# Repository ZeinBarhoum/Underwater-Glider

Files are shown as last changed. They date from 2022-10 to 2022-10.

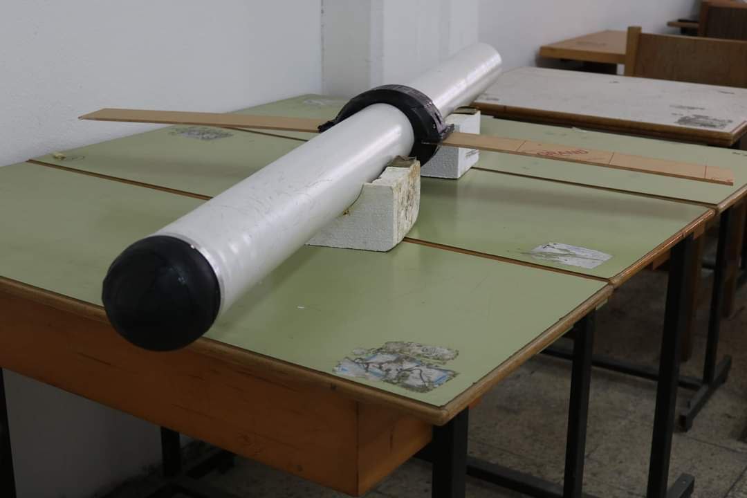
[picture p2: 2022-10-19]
Underwater glider.jpg

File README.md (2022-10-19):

# Underwater-Glider

This repository includes the design and source code files for the project "Underwater Glider"

Underwater gliders are underwater vehicles that don’t use any external propellers or thrusters.  

These vehicles are autonomous, and their motion depends on controlling the buoyancy-gravity force balance and the placement of the center of gravity.

Buoyancy is controlled using buoyancy engine (BE) which could operate in one of two ways:
  1-	Varying the mass of the vehicle by inhaling or exhaling the surrounding fluid (water).
  2-	Varying the volume of the vehicle by inflating or deflating an external balloon-shaped bladder
  
The BE used in this project is from the first type, and a tank is designed using syringes to accomplish this functionality.

To control the center of gravity, a moving mass (MM) system was designed which can change the center of gravity along the main axis by sliding the mass, and to change the center of gravity on the YZ plane, rotating the mass was the method of choice.

A full study and implementation were conducted in this project starting from designing, modeling and simulating and ending with manifacturing, testing and controling the underwater glider.

All the files are included in the repository and for further information please contact the authors of this project.

Zein Alabedeen Barhoum: zein.barhoum799@gmail.com
Rahaf Alshaowa: rahafalshaowa98@gmail.com

Note: this project was conducted to fulfill the requirements of Bachelor's degree in mechatronics engineering. And based on the implementation, report and presentation, a grade with honor of 96% was awarded to the authors of this project.

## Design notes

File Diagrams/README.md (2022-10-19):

# diagrams

In this folder, the pinout diagram of the circuit of the underwater glider is provided with specific diagrams for each electronic component used.
Three stepper were used with sizing of NEMA17, A4988 circuits were used (3 of them, one for each motor).
four hand-made leakage sensors were used in the two endings and the center of the glider. Moreover, limit switches were used to prevent the mechanical part from stepping out of their limits mechanically, two were used for each motor. 
As stated before, the beaglebone blue was used as the main controller, an therefore, its pinout diagram is provided.

Two power systems were used in the glider, one is 12V for the motors and the beaglebone. And 5V system for sensors and to provide power in the case of power outage in the 12V system.
The batteries used in addition to the charging circuits are shown in diagrams too.

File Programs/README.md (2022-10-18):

# Simulink Programs

the controller used in the underwater glider is the beaglebone blue which has an intertial measurment unit (IMU) which is the MPU-9250 that includes 
gyroscope,accelerometer and magnetometer. Moreover, an additional IMU which is the MPU-6050 was used. A fusion algorithm between these two IMUs were used to 
calculate the angular position (using Euler angles), in addition, the acceleration were also calculated to test depth calculation using acceleration data. 
The programs that were used to control the underwater glider were constructed using Simulink software with the beaglebone blue plugin.

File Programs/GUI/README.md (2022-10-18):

# GUI

An expermental GUI was created using MATLAB which interactc with the Simulink program to visualize the current position of the glider.

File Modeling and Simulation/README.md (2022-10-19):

# Modeling and Simulation

A modeling of the designed underwater glider was conducted, the mathmatical equations that formulate the motion of the vehicle depending on the 
input on the motor were analyzed and inputed into Matlab and Simulink to simulate the motion of the underwater glider under diffrent inputs.

The full model and simulation files are provided here.

Note: the Initialize.m file compute the symbolic inverse of multiple matrices in the model in order to avoid run-time calculations of matrix-inverse 
this dramatically decreases the time of the simulation.

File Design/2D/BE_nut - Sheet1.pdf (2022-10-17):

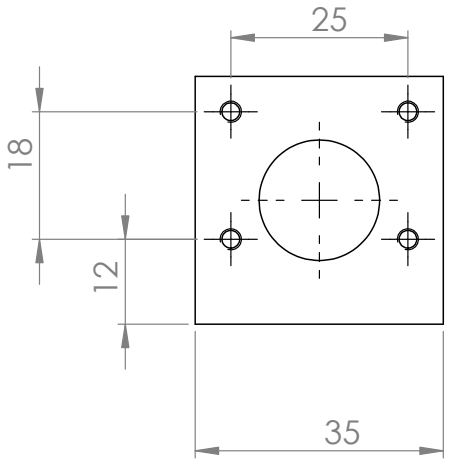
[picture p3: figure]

35

20

47

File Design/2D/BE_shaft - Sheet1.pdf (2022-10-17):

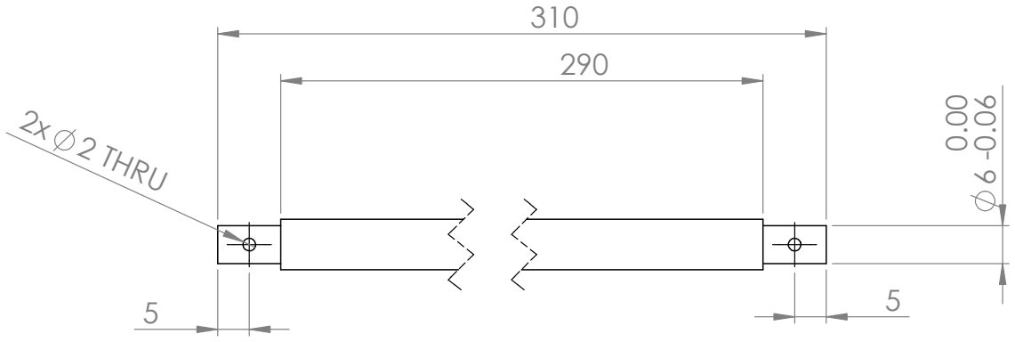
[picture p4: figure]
2 THRU

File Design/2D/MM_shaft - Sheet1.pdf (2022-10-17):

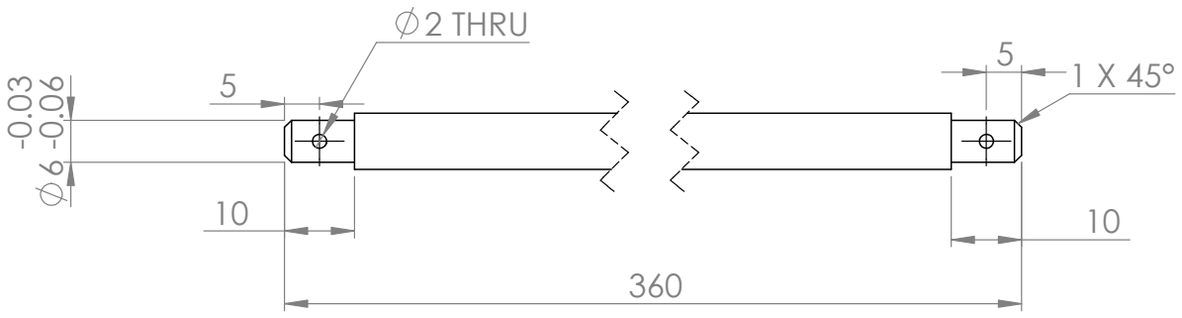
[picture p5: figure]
2 THRU

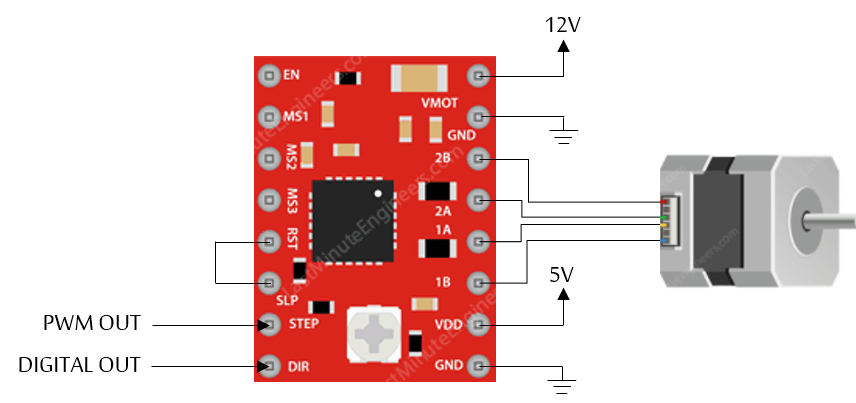
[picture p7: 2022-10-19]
Diagrams/A4988.png

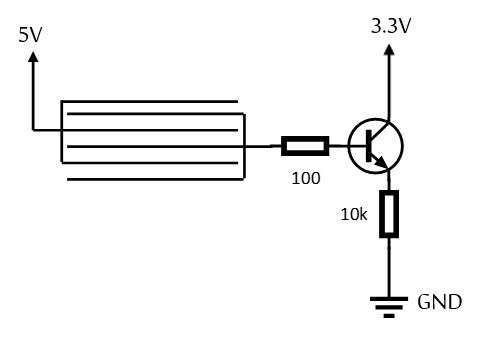
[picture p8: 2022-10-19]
Diagrams/leak sensor.png

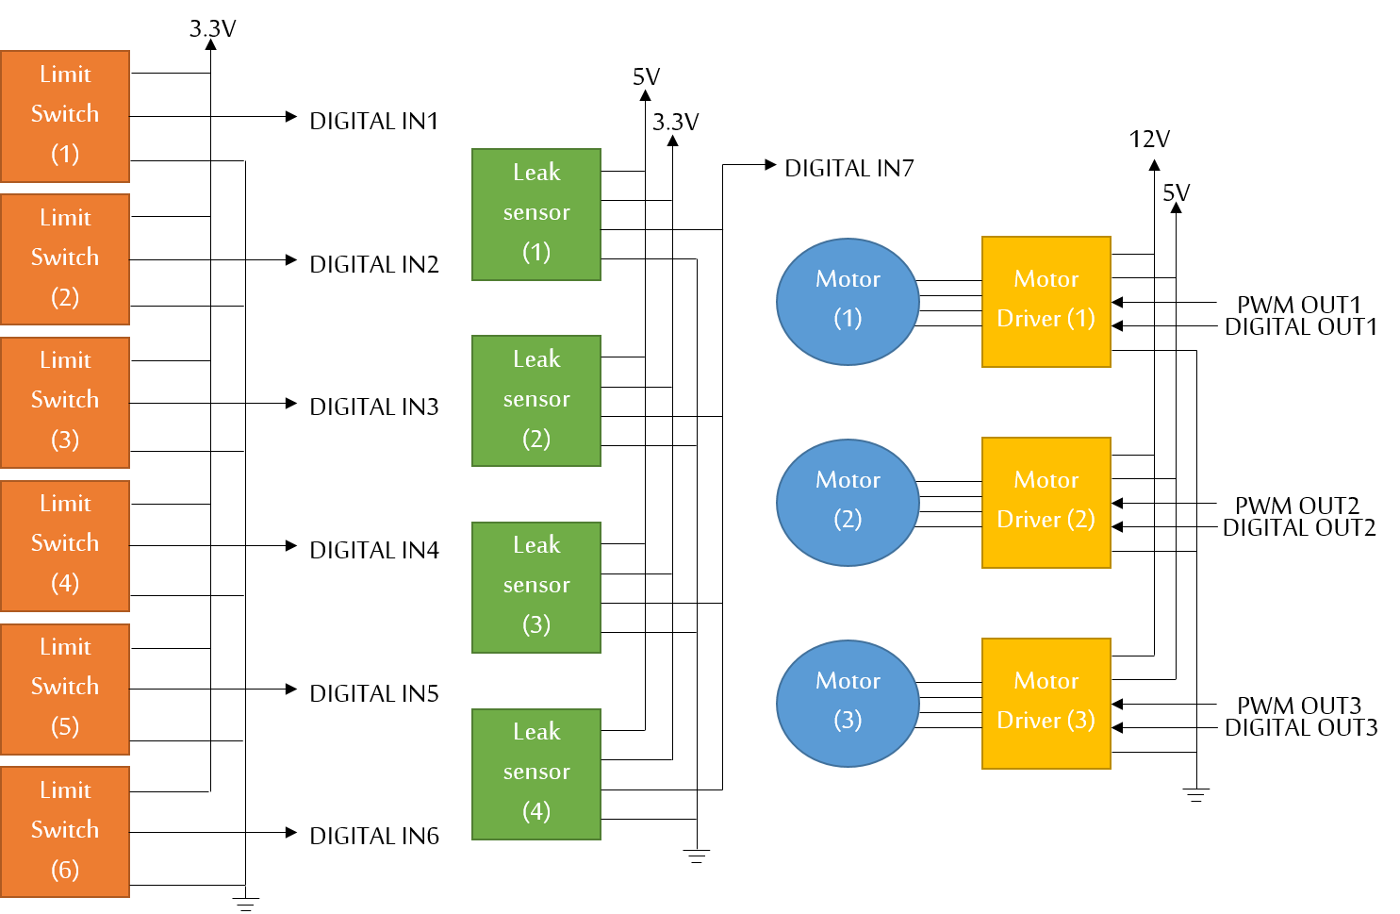
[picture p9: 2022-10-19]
Diagrams/all1.png

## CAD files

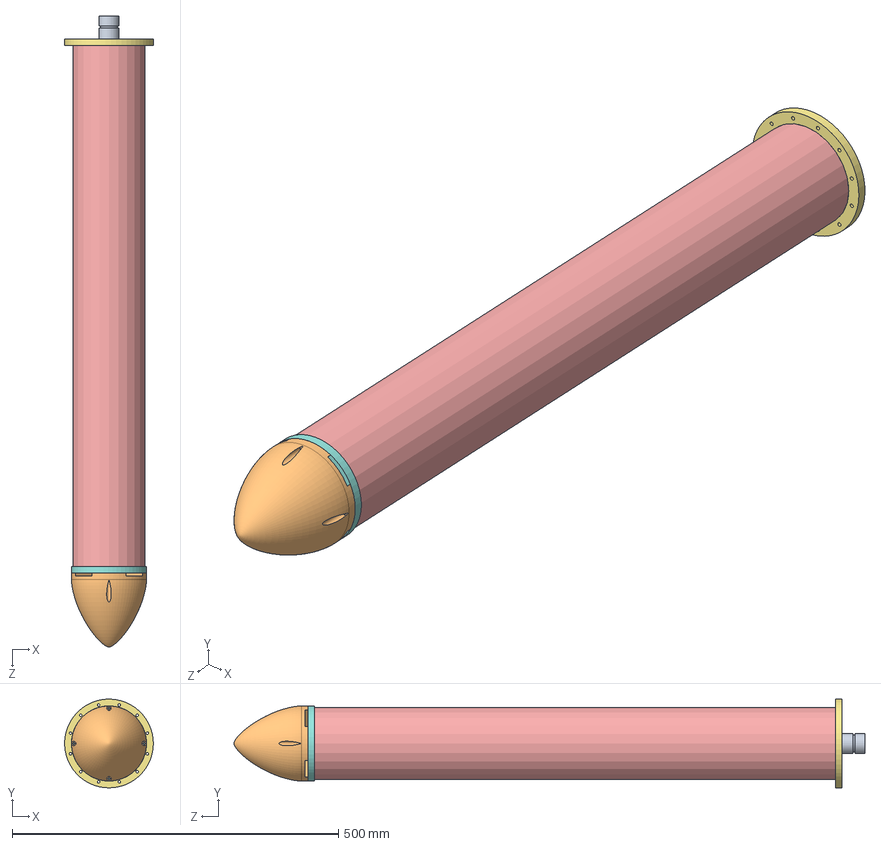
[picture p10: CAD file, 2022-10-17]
Design/BE_MAIN.SLDASM
135.9 x 135.9 x 966.6 mm
BE_stepper_disk
NEMA17_double
BE_5x5coupler
BE_construct x 3
BE_fix_thread x 18
BE_TH
angular contact ball bearing_68_iso x 2
BE_static_1
BE_shaft
syringe piston x 3
BE_moving_1
BE_nut
BE_smooth x 2
BE_static_2
syringe cylinder x 3
BE_static_3
BE_static_4
CU_BeagleBoneBlue
CU_static x 2
CU_BBbase
CU_BatteryBase
CU_BatteryCase x 4
CE_board
CE_battery x 8
SE_One_flange
SE_tube1 x 2
SE_tube2
o-rings ai x 3
SE_mid_flange
SE_head2
SE_head1
middle2
head
water pipe x 3

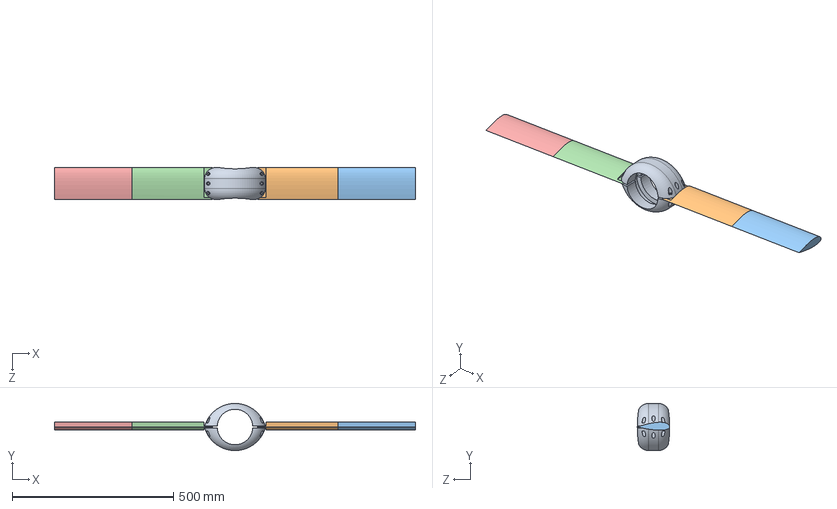
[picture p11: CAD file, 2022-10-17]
Design/Wing_Assembly.SLDASM
1118.1 x 146.0 x 100.0 mm
fixWings2 x 2
Wing1_1
Wing1_2
Wing2_1
Wing2_2

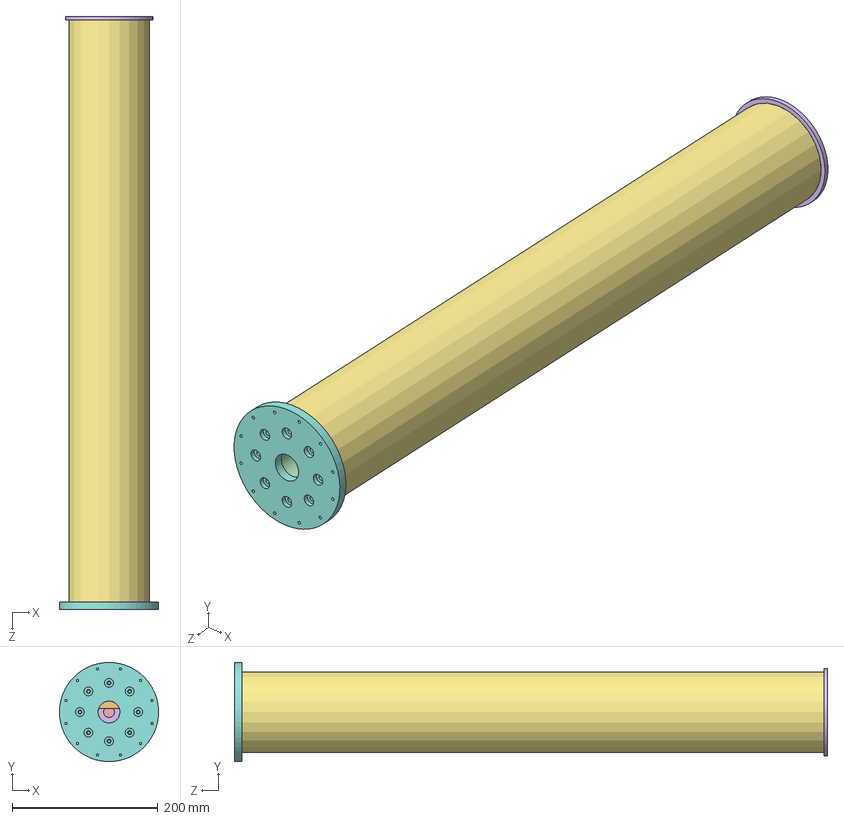
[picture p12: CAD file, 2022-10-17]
Design/MM_Main.SLDASM
135.9 x 135.9 x 813.0 mm
MM_moving_stepper_disk
MM_NEMA_17 x 2
MM_5x5coupler x 2
MM_Mass_shaft2
MM_Mass_handle x 2
MM_Mass
MM_Mass_shaft
MM_moving_disk
MM_moving_disk2
MM_shft_screw_nut
MM_moving_construct x 4
MM_moving_fix_thread x 12
MM_static2.2 x 2
MM_static_stepper
MM_shaft_extend
MM_shaft
MM_shaft_extend_long
MM_construct x 3
MM_fix x 9
SE_mid_flange
SE_end_flange - Copy
SE_head3
SE_head2.2
o-rings ai x 4
angular contact ball bearing_68_iso x 4
MM_smooth x 6

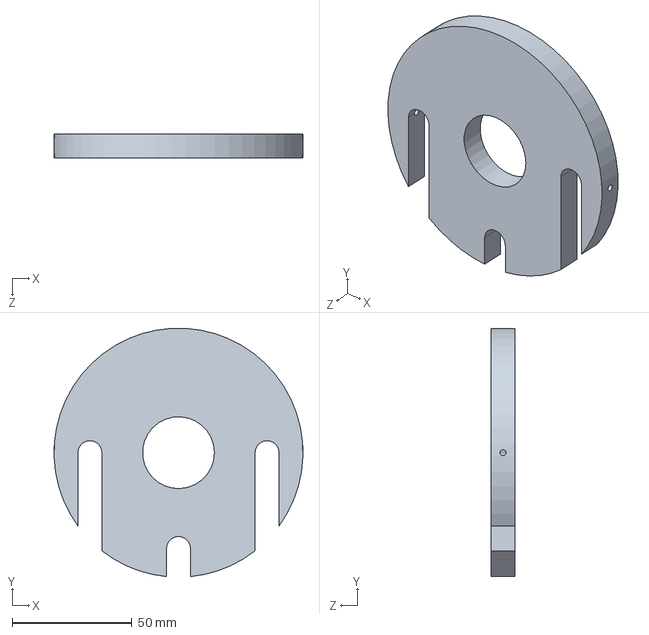
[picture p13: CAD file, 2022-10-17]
Design/masses3.SLDPRT
104.0 x 103.7 x 10.0 mm

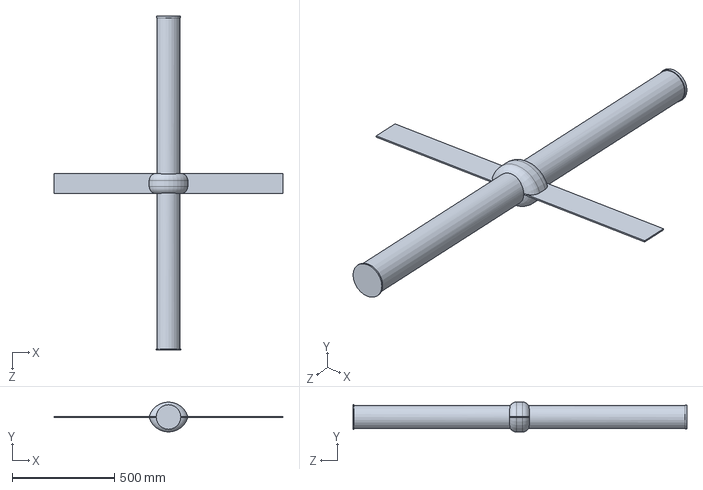
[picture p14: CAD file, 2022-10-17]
Hydrodynamic Study/design outer/plain.SLDPRT
1118.5 x 146.4 x 1631.0 mm

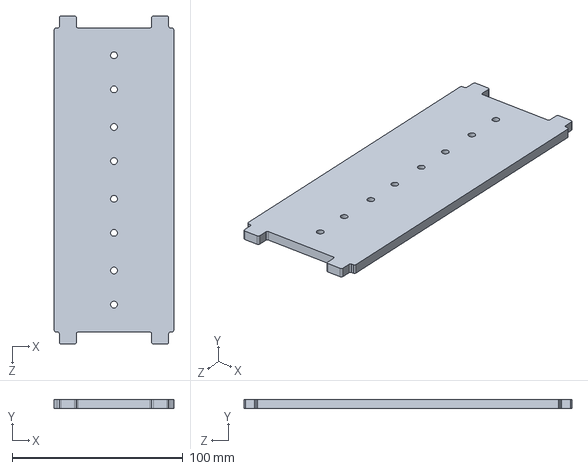
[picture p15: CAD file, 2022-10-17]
Design/CU_BatteryBase.SLDPRT
70.0 x 5.00 x 192.0 mm

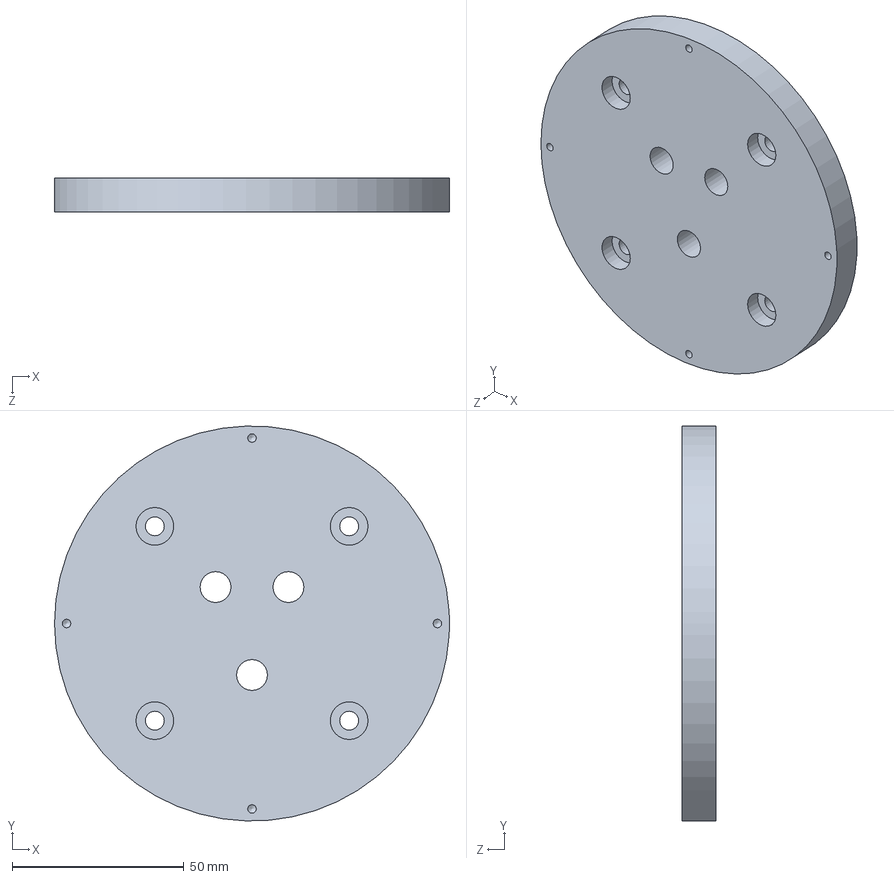
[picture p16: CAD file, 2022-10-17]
Design/NEW/SE_head1.SLDPRT
115.0 x 114.9 x 10.0 mm

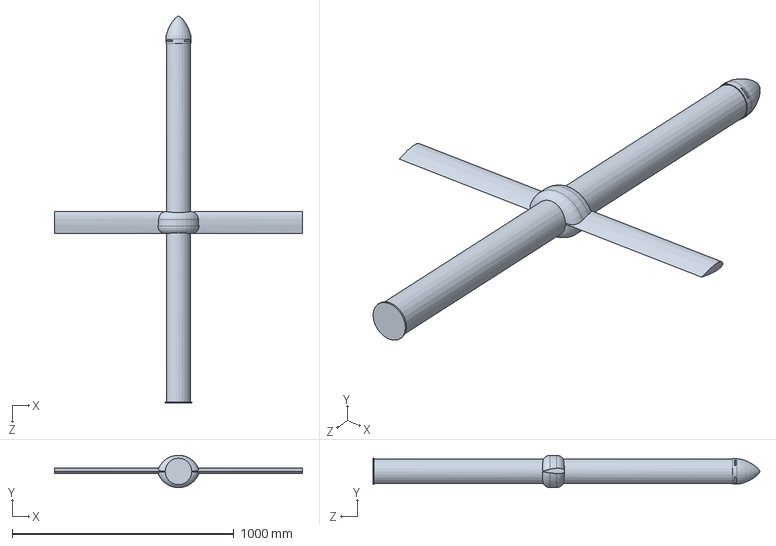
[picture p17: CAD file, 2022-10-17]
Hydrodynamic Study/design outer/head+wings.SLDPRT
1118.5 x 145.8 x 1744.7 mm

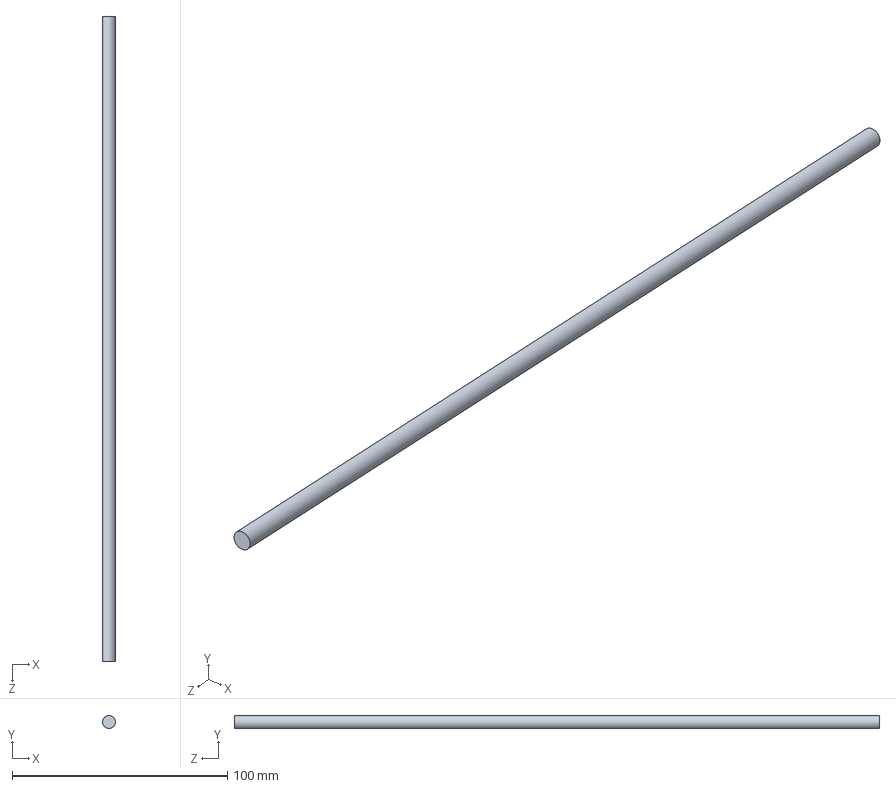
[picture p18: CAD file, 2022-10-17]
Design/MM_moving_construct.SLDPRT
6.00 x 6.00 x 300.0 mm

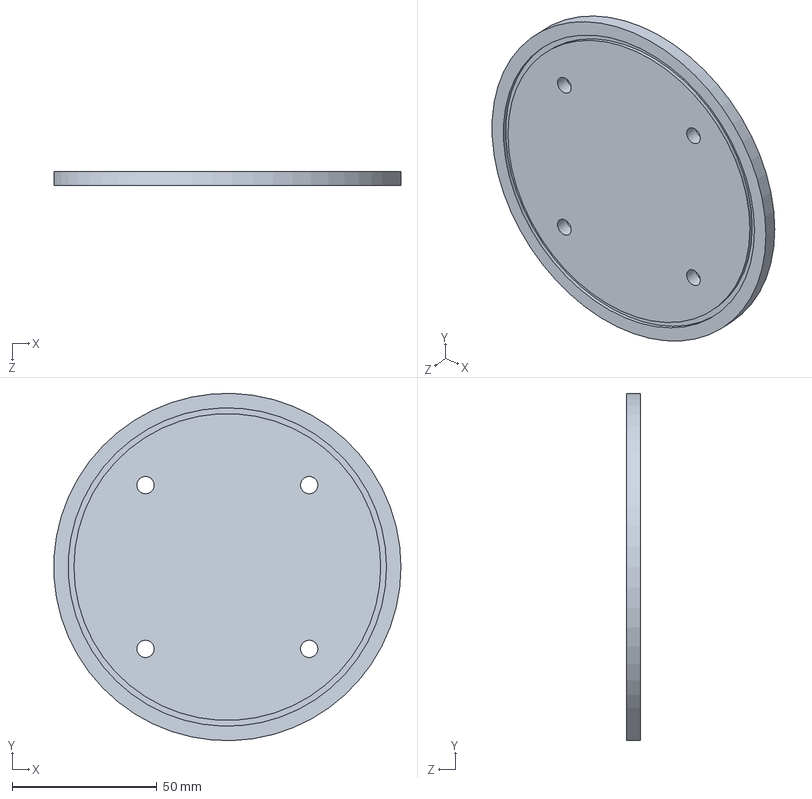
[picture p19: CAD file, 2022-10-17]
Design/NEW/SE_head3.SLDPRT
119.9 x 119.9 x 5.00 mm

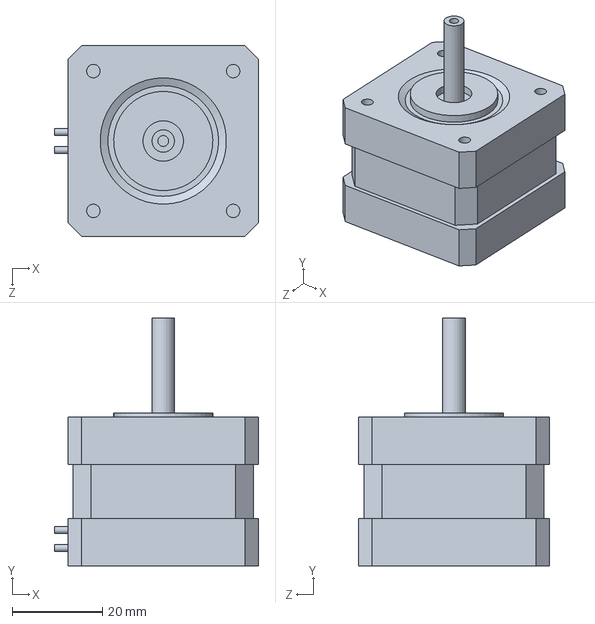
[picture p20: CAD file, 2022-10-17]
Design/MM_NEMA_17.SLDPRT
45.3 x 55.0 x 42.3 mm

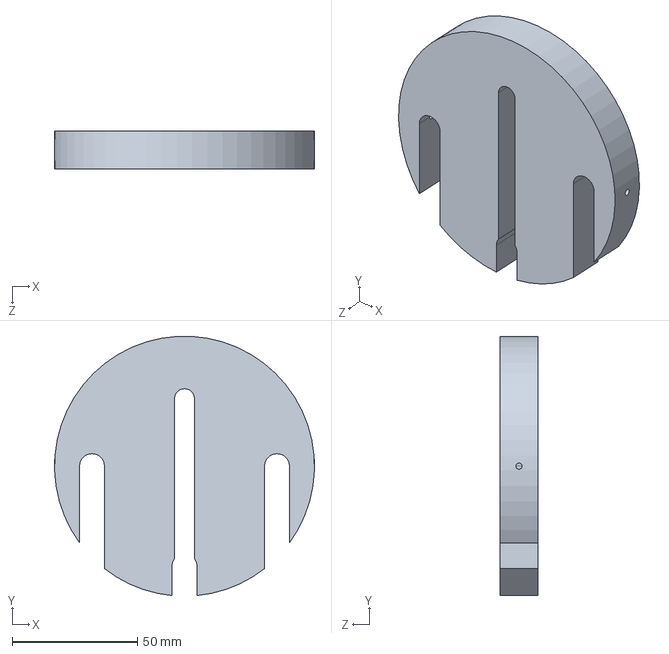
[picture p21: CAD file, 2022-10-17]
Design/NEW/masses.SLDPRT
104.0 x 103.7 x 15.0 mm

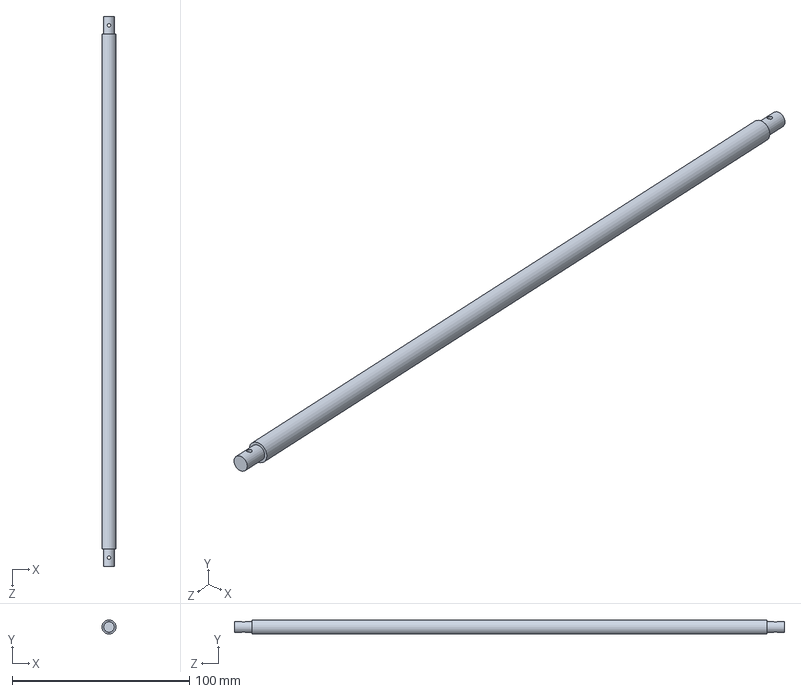
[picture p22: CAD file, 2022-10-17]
Design/BE_shaft.SLDPRT
8.00 x 8.00 x 310.0 mm

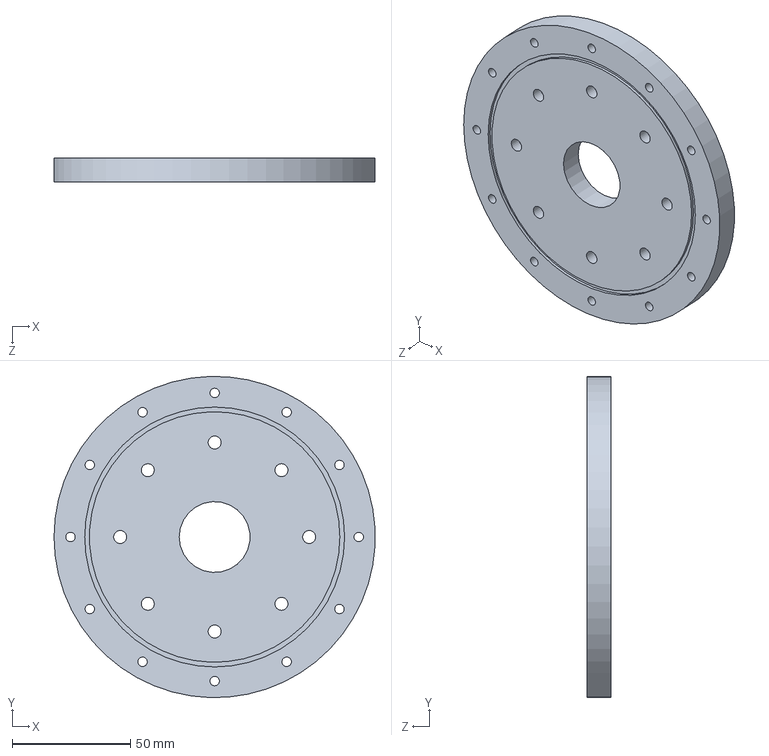
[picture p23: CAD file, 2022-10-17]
Design/NEW/SE_head2.SLDPRT
135.9 x 135.9 x 10.0 mm

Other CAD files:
Design/NEW/masses3.SLDPRT
Hydrodynamic Study/design outer/wings .SLDPRT
Hydrodynamic Study/design outer/head .SLDPRT
Design/BE_static_2.SLDPRT
Design/BE-OMRON V-155-1A5.SLDPRT
Design/BE_5x5coupler.SLDPRT
Design/BE_TH.SLDPRT
Design/BE_construct.SLDPRT
Design/BE_fix_thread.SLDPRT
Design/BE_hold2.SLDPRT
Design/BE_moving_1.SLDPRT
Design/BE_nut.SLDPRT
Design/BE_smooth.SLDPRT
Design/BE_static_1.SLDPRT
Design/BE_static_3.SLDPRT
Design/BE_static_4.SLDPRT
Design/BE_stepper_disk.SLDPRT
Design/CE_battery.SLDPRT
Design/CE_board.SLDPRT
Design/CU_BBbase.SLDPRT
Design/CU_BBbasefix.SLDPRT
Design/CU_BatteryCase.SLDPRT
Design/CU_static.SLDPRT
Design/MM-OMRON V-155-1A5.SLDPRT
Design/MM_5x5coupler.SLDPRT
Design/MM_Mass.SLDPRT
Design/MM_Mass_handle.SLDPRT
Design/MM_Mass_shaft.SLDPRT
Design/MM_Mass_shaft2.SLDPRT
Design/MM_construct.SLDPRT
Design/MM_fix.SLDPRT
Design/MM_moving_disk.SLDPRT
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

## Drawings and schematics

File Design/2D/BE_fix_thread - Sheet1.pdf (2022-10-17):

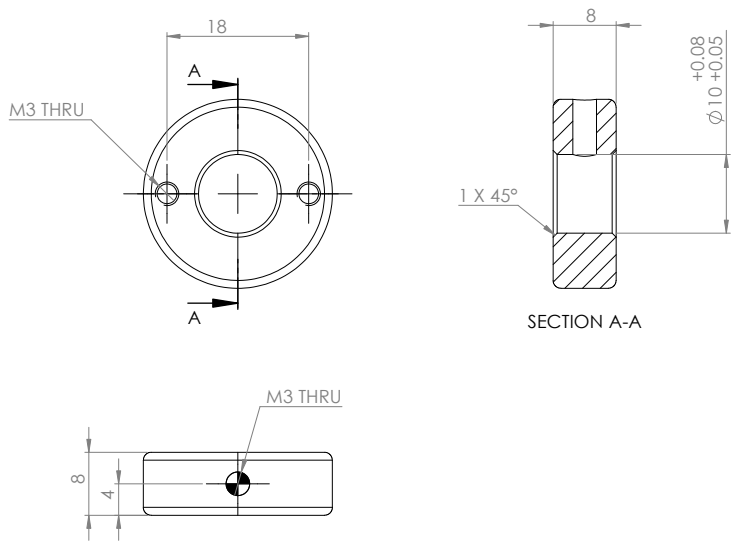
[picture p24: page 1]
M3 THRU; SECTION A-A

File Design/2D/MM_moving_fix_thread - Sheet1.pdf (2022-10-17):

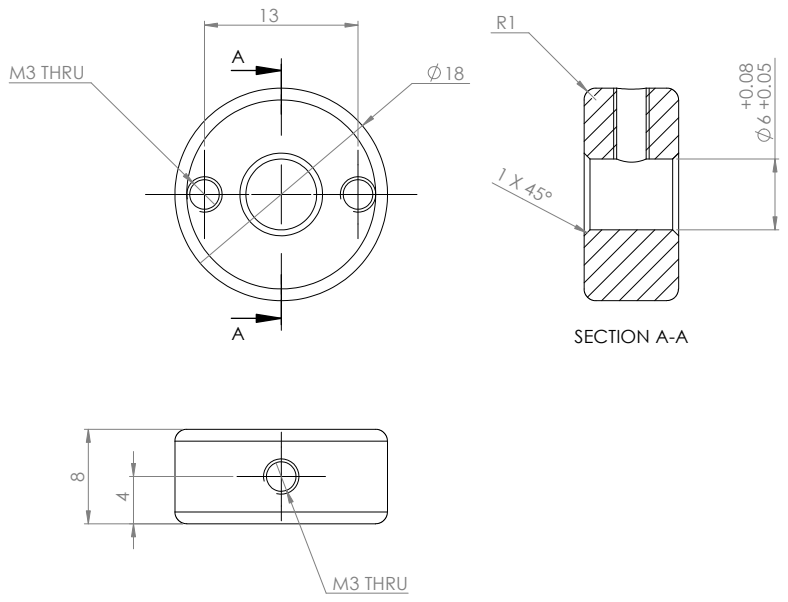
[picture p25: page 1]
M3 THRU; SECTION A-A

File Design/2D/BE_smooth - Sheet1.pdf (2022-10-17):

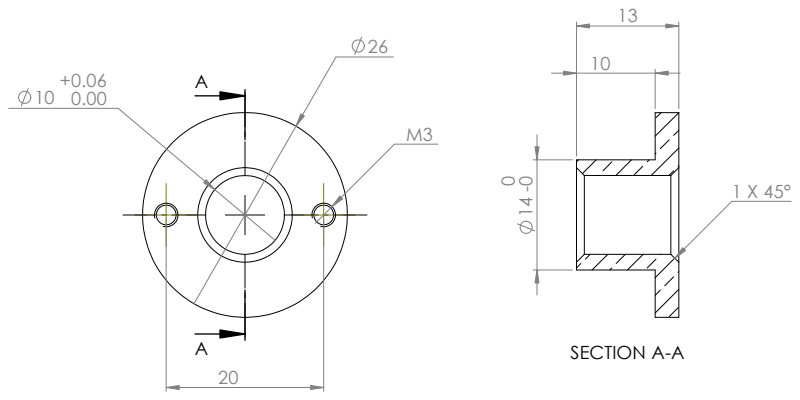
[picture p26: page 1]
SECTION A-A

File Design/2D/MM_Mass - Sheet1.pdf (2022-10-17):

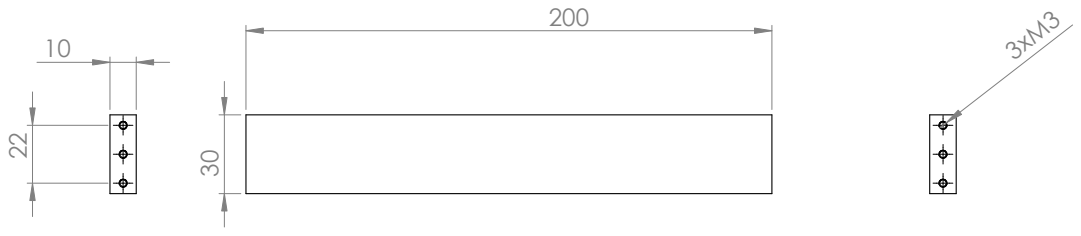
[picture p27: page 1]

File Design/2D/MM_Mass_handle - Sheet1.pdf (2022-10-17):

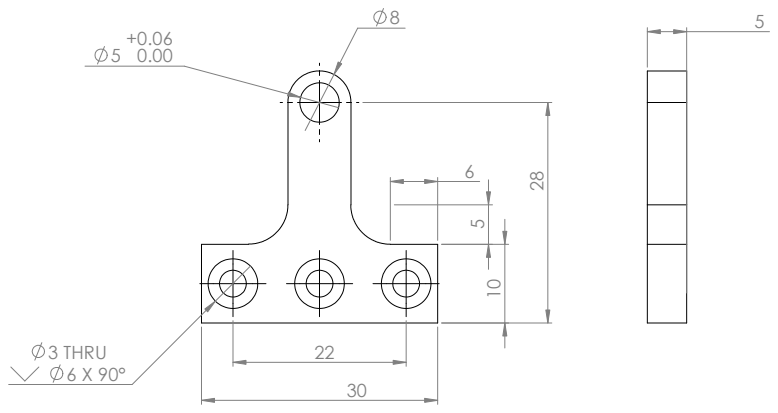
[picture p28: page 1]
3 THRU

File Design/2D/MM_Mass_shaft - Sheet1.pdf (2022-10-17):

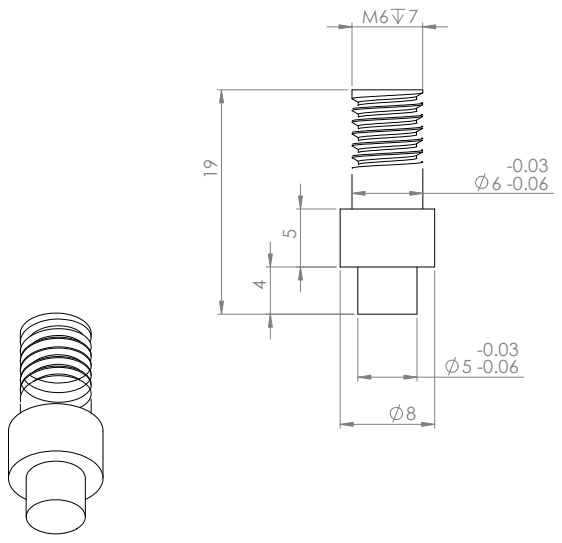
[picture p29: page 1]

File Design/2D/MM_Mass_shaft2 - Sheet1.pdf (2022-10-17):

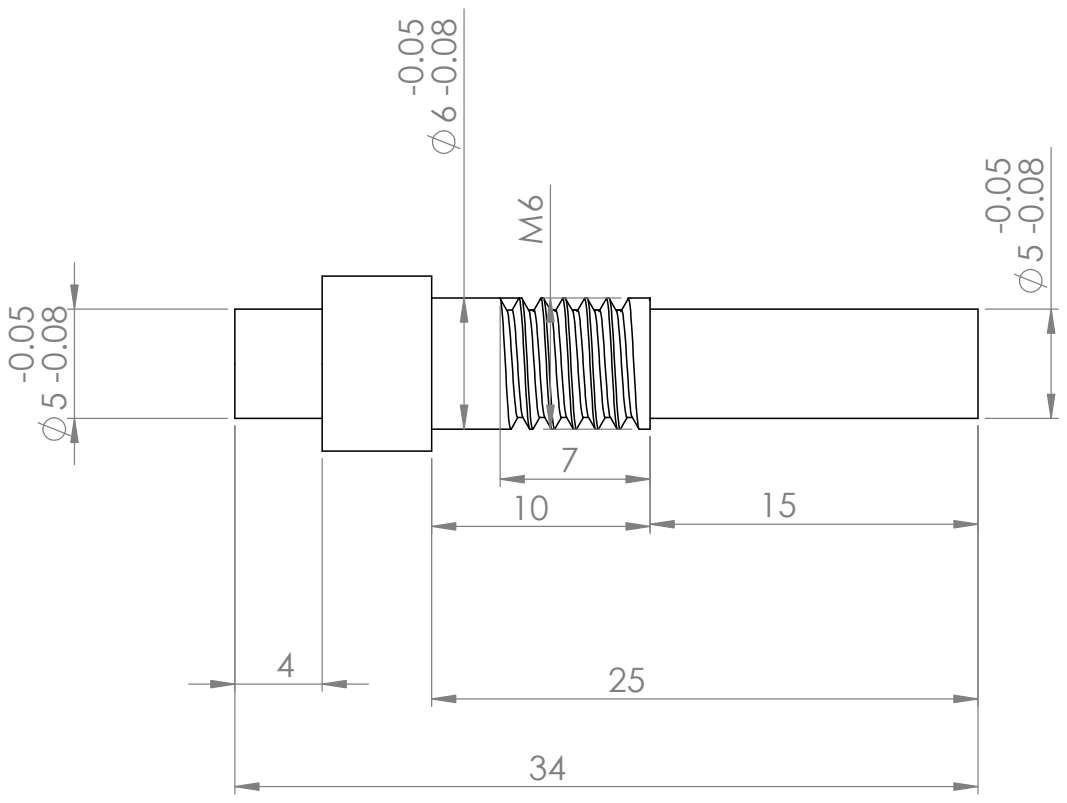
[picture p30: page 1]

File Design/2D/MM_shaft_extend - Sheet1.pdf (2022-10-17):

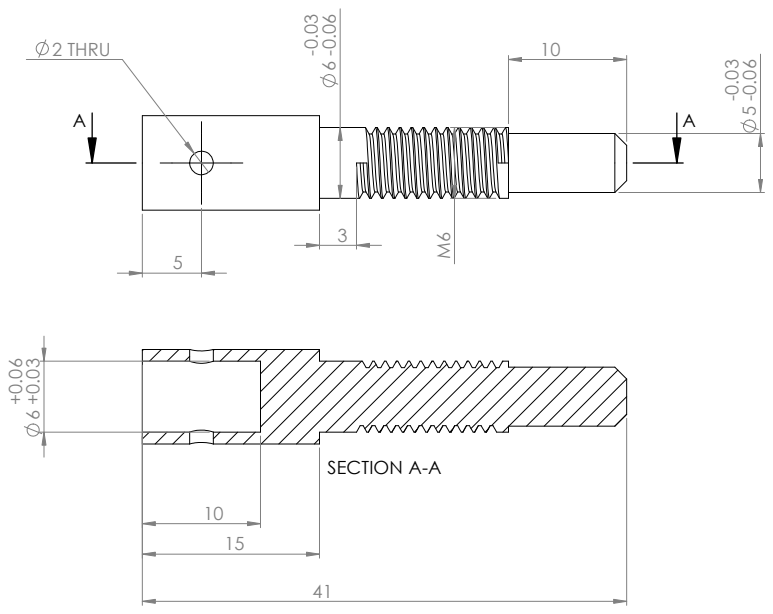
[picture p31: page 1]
2 THRU; SECTION A-A

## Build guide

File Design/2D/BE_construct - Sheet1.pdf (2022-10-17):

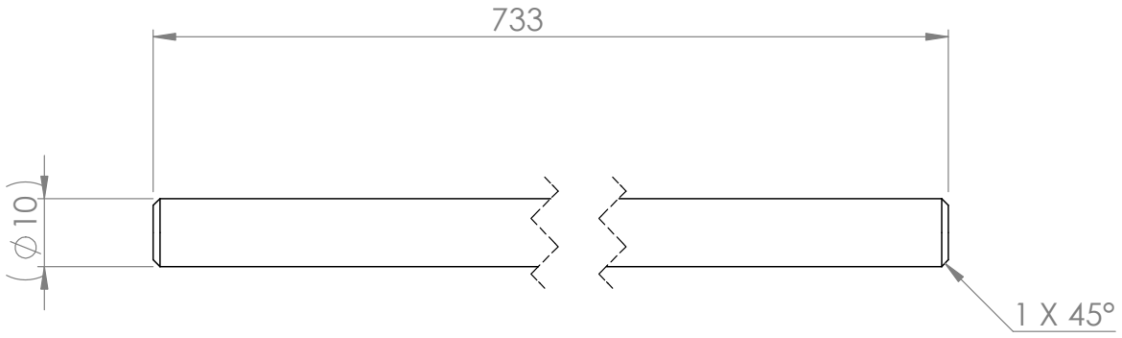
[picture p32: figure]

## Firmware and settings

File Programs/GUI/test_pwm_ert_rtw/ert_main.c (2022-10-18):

/*
 * File: ert_main.c
 *
 * Code generated for Simulink model 'test_pwm'.
 *
 * Model version                  : 1.3
 * Simulink Coder version         : 9.4 (R2020b) 29-Jul-2020
 * C/C++ source code generated on : Thu Jun  3 13:57:14 2021
 *
 * Target selection: ert.tlc
 * Embedded hardware selection: ARM Compatible->ARM Cortex
 * Code generation objectives: Unspecified
 * Validation result: Not run
 */

#include <stdio.h>
#include <stdlib.h>
#include "test_pwm.h"
#include "test_pwm_private.h"
#include "rtwtypes.h"
#include "limits.h"
#include "rt_nonfinite.h"
#include "MW_bbblue_init.h"
#include "linuxinitialize.h"
#define UNUSED(x)                      x = x
#define NAMELEN                        16

/* Function prototype declaration*/
void exitFcn(int sig);
void *terminateTask(void *arg);
void *baseRateTask(void *arg);
void *subrateTask(void *arg);
volatile boolean_T stopRequested = false;
volatile boolean_T runModel = true;
sem_t stopSem;
sem_t baserateTaskSem;
pthread_t schedulerThread;
pthread_t baseRateThread;
void *threadJoinStatus;
int terminatingmodel = 0;
void *baseRateTask(void *arg)
{
  runModel = (rtmGetErrorStatus(test_pwm_M) == (NULL)) && !rtmGetStopRequested
    (test_pwm_M);
  while (runModel) {
    sem_wait(&baserateTaskSem);

    /* External mode */
    {
      boolean_T rtmStopReq = false;
      rtExtModePauseIfNeeded(test_pwm_M->extModeInfo, 1, &rtmStopReq);
      if (rtmStopReq) {
        rtmSetStopRequested(test_pwm_M, true);
      }

      if (rtmGetStopRequested(test_pwm_M) == true) {
        rtmSetErrorStatus(test_pwm_M, "Simulation finished");
        break;
      }
    }

    /* External mode */
    {
      boolean_T rtmStopReq = false;
      rtExtModeOneStep(test_pwm_M->extModeInfo, 1, &rtmStopReq);
      if (rtmStopReq) {
        rtmSetStopRequested(test_pwm_M, true);
      }
    }

    test_pwm_step();

    /* Get model outputs here */
    rtExtModeCheckEndTrigger();
    stopRequested = !((rtmGetErrorStatus(test_pwm_M) == (NULL)) &&
                      !rtmGetStopRequested(test_pwm_M));
    runModel = !stopRequested;
  }

  runModel = 0;
  terminateTask(arg);
  pthread_exit((void *)0);
  return NULL;
}

void exitFcn(int sig)
{
  UNUSED(sig);
  rtmSetErrorStatus(test_pwm_M, "stopping the model");
  runModel = 0;
}

void *terminateTask(void *arg)
{
  UNUSED(arg);
  terminatingmodel = 1;

  {
    runModel = 0;
  }

  MW_bbblue_terminate();

  /* Disable rt_OneStep() here */

  /* Terminate model */
  test_pwm_terminate();
  rtExtModeShutdown(1);
  sem_post(&stopSem);
  return NULL;
}

int main(int argc, char **argv)
{
  UNUSED(argc);
  UNUSED(argv);
  MW_bbblue_init();
  rtmSetErrorStatus(test_pwm_M, 0);
  rtExtModeParseArgs(argc, (const char_T **)argv, NULL);

  /* Initialize model */
  test_pwm_initialize();

  /* External mode */
  rtSetTFinalForExtMode(&rtmGetTFinal(test_pwm_M));
  rtExtModeCheckInit(1);

  {
    boolean_T rtmStopReq = false;
    rtExtModeWaitForStartPkt(test_pwm_M->extModeInfo, 1, &rtmStopReq);
    if (rtmStopReq) {
      rtmSetStopRequested(test_pwm_M, true);
    }
  }

  rtERTExtModeStartMsg();

  /* Call RTOS Initialization function */
  myRTOSInit(0.0002, 0);

  /* Wait for stop semaphore */
  sem_wait(&stopSem);

#if (MW_NUMBER_TIMER_DRIVEN_TASKS > 0)

  {
    int i;
    for (i=0; i < MW_NUMBER_TIMER_DRIVEN_TASKS; i++) {
      CHECK_STATUS(sem_destroy(&timerTaskSem[i]), 0, "sem_destroy");
    }
  }

#endif

  return 0;
}

/*
 * File trailer for generated code.
 *
 * [EOF]
 */

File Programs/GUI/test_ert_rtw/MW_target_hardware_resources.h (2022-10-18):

#ifndef PORTABLE_WORDSIZES
#ifdef __MW_TARGET_USE_HARDWARE_RESOURCES_H__
#ifndef __MW_TARGET_HARDWARE_RESOURCES_H__
#define __MW_TARGET_HARDWARE_RESOURCES_H__

#define MW_MULTI_TASKING_MODE 1
#include "MW_bbblue_init.h"

#define MW_USECODERTARGET 1
#define MW_TARGETHARDWARE BeagleBone Blue
#define MW_CONNECTIONINFO_TCPIP_IPADDRESS codertarget.bbblue.getDeviceAddress
#define MW_CONNECTIONINFO_TCPIP_PORT 17725
#define MW_CONNECTIONINFO_TCPIP_VERBOSE 0
#define MW_CONNECTIONINFO_TCPIP_RUNINBACKGROUND 0
#define MW_EXTMODE_CONFIGURATION TCP/IP
#define MW_EXTMODE_RUNNING on
#define MW_RTOS Linux
#define MW_RTOSBASERATETASKPRIORITY 40
#define MW_DETECTTASKOVERRUNS 0.000000
#define MW_SCHEDULER_INTERRUPT_SOURCE 0
#define MW_BOARDPARAMETERS_DEVICEADDRESS 192.168.1.100
#define MW_BOARDPARAMETERS_USERNAME debian
#define MW_BOARDPARAMETERS_PASSWORD temp1234
#define MW_BOARDPARAMETERS_BUILDDIR /home/debian
#define MW_RUNTIME_BUILDACTION -1
#define MW_DATAVERSION 2016.02

#endif /* __MW_TARGET_HARDWARE_RESOURCES_H__ */

#endif

#endif

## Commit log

2022-10-17 Add Design Files
    [BE-OMRON V-155-1A5.SLDPRT, BE_5x5coupler.SLDPRT, BE_MAIN.SLDASM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]
2022-10-17 Add Hydrodynamic Files
    [DesignPointLog.csv, head .SLDPRT, head+wings.SLDPRT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]
